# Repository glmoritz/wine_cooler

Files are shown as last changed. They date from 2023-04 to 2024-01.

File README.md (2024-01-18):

# wine_cooler
UPDATE: The hardware is working using this PID script -> https://github.com/glmoritz/tasmota_berry_pid

Control board replacement for an Electrolux Wine Cooler (https://loja.electrolux.com.br/adega-elctrolux--8-garrafas-1-porta-preta-acabamento-em-aluminio---acb08-/p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)

The original control board for this wine cooler is a SH14387 board which is known to present failures during its lifespan. So, instead of ordering a new one for my broken wine cooler I decided to build my own control board using cheap aliexpress components.

The controller will be based on ESP32 Devboard C. This way I can run Tasmota in Thermostat mode and set/monitor all Cooler parameters using MQTT. Tasmota seamslessy integrates with Home Assistant, this way I will have very little work in firmware programming (just recompiling and configuring Tasmota with the correct parameters and then adding the device to Home Assistant).

Tasmota thermostat is very capable. It uses a mixed on/off PID strategy which seems to work well. Time will tell...

Board features:

- The board expects a 12V@6A input, which can be provided by a simple COTS power source.

- Controlled 12V 5A output for driving the peltier board.

- 2x Controlled 12V 200mA output for driving the cold/hot peltier fans.

- 10k NTC input for reading the built in Cooler NTC 

- DS1820 input (https://pt.aliexpress.com/item/4000895660165.html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)

This will be the Thermostat feedback sensor. The built in sensor is installed directly on peltier cell which is always colder than the cooler interior. I am planning to install the DS1820 nearer to the bottles to have a more precise temperature control.

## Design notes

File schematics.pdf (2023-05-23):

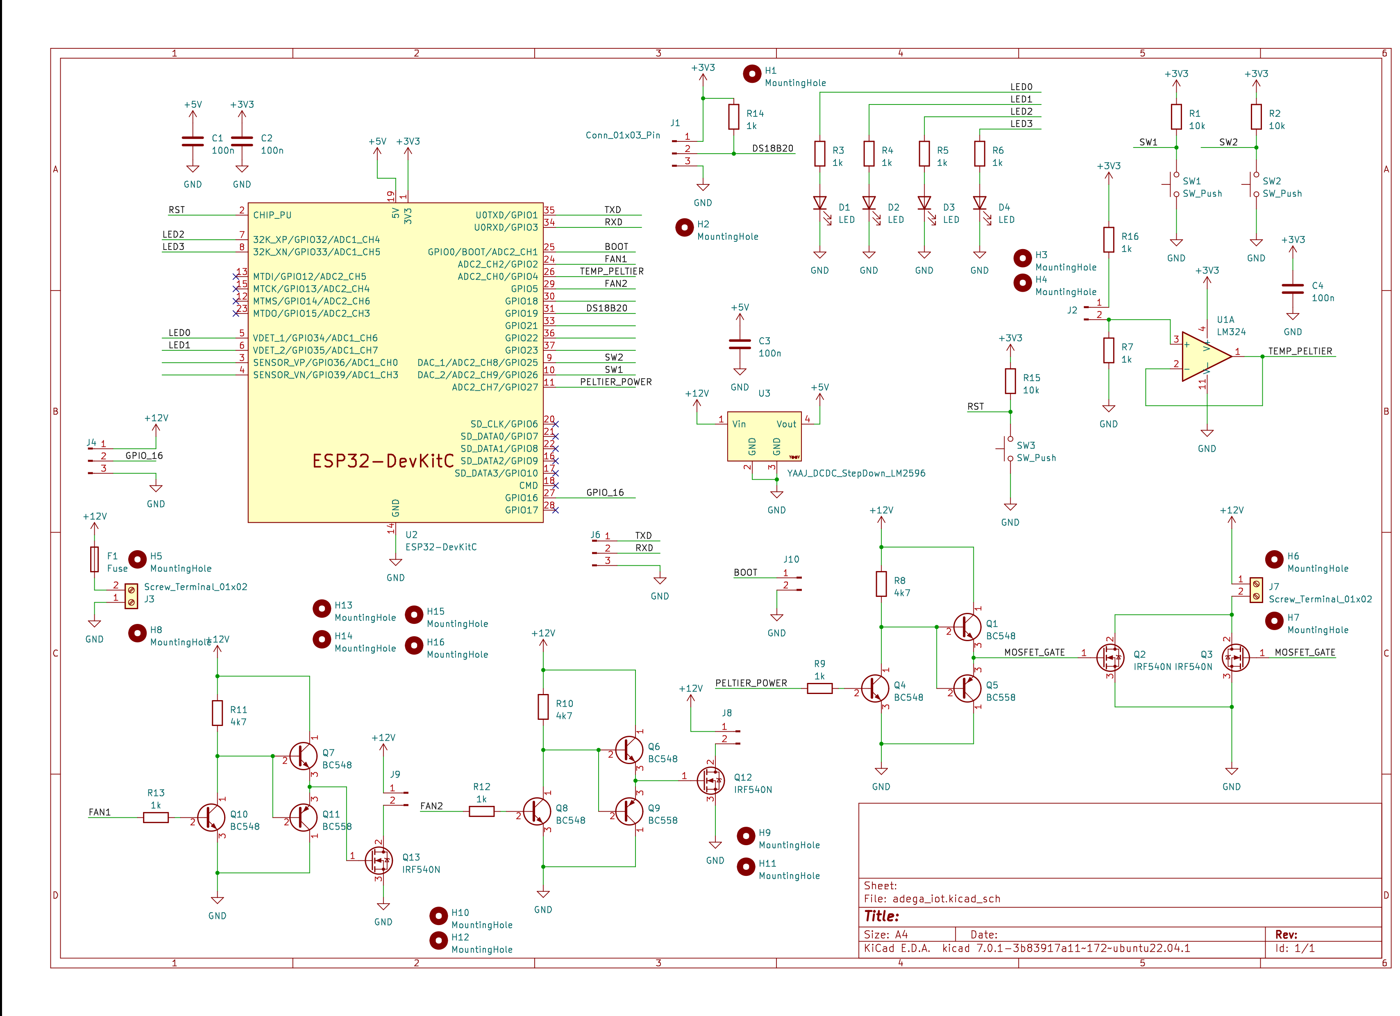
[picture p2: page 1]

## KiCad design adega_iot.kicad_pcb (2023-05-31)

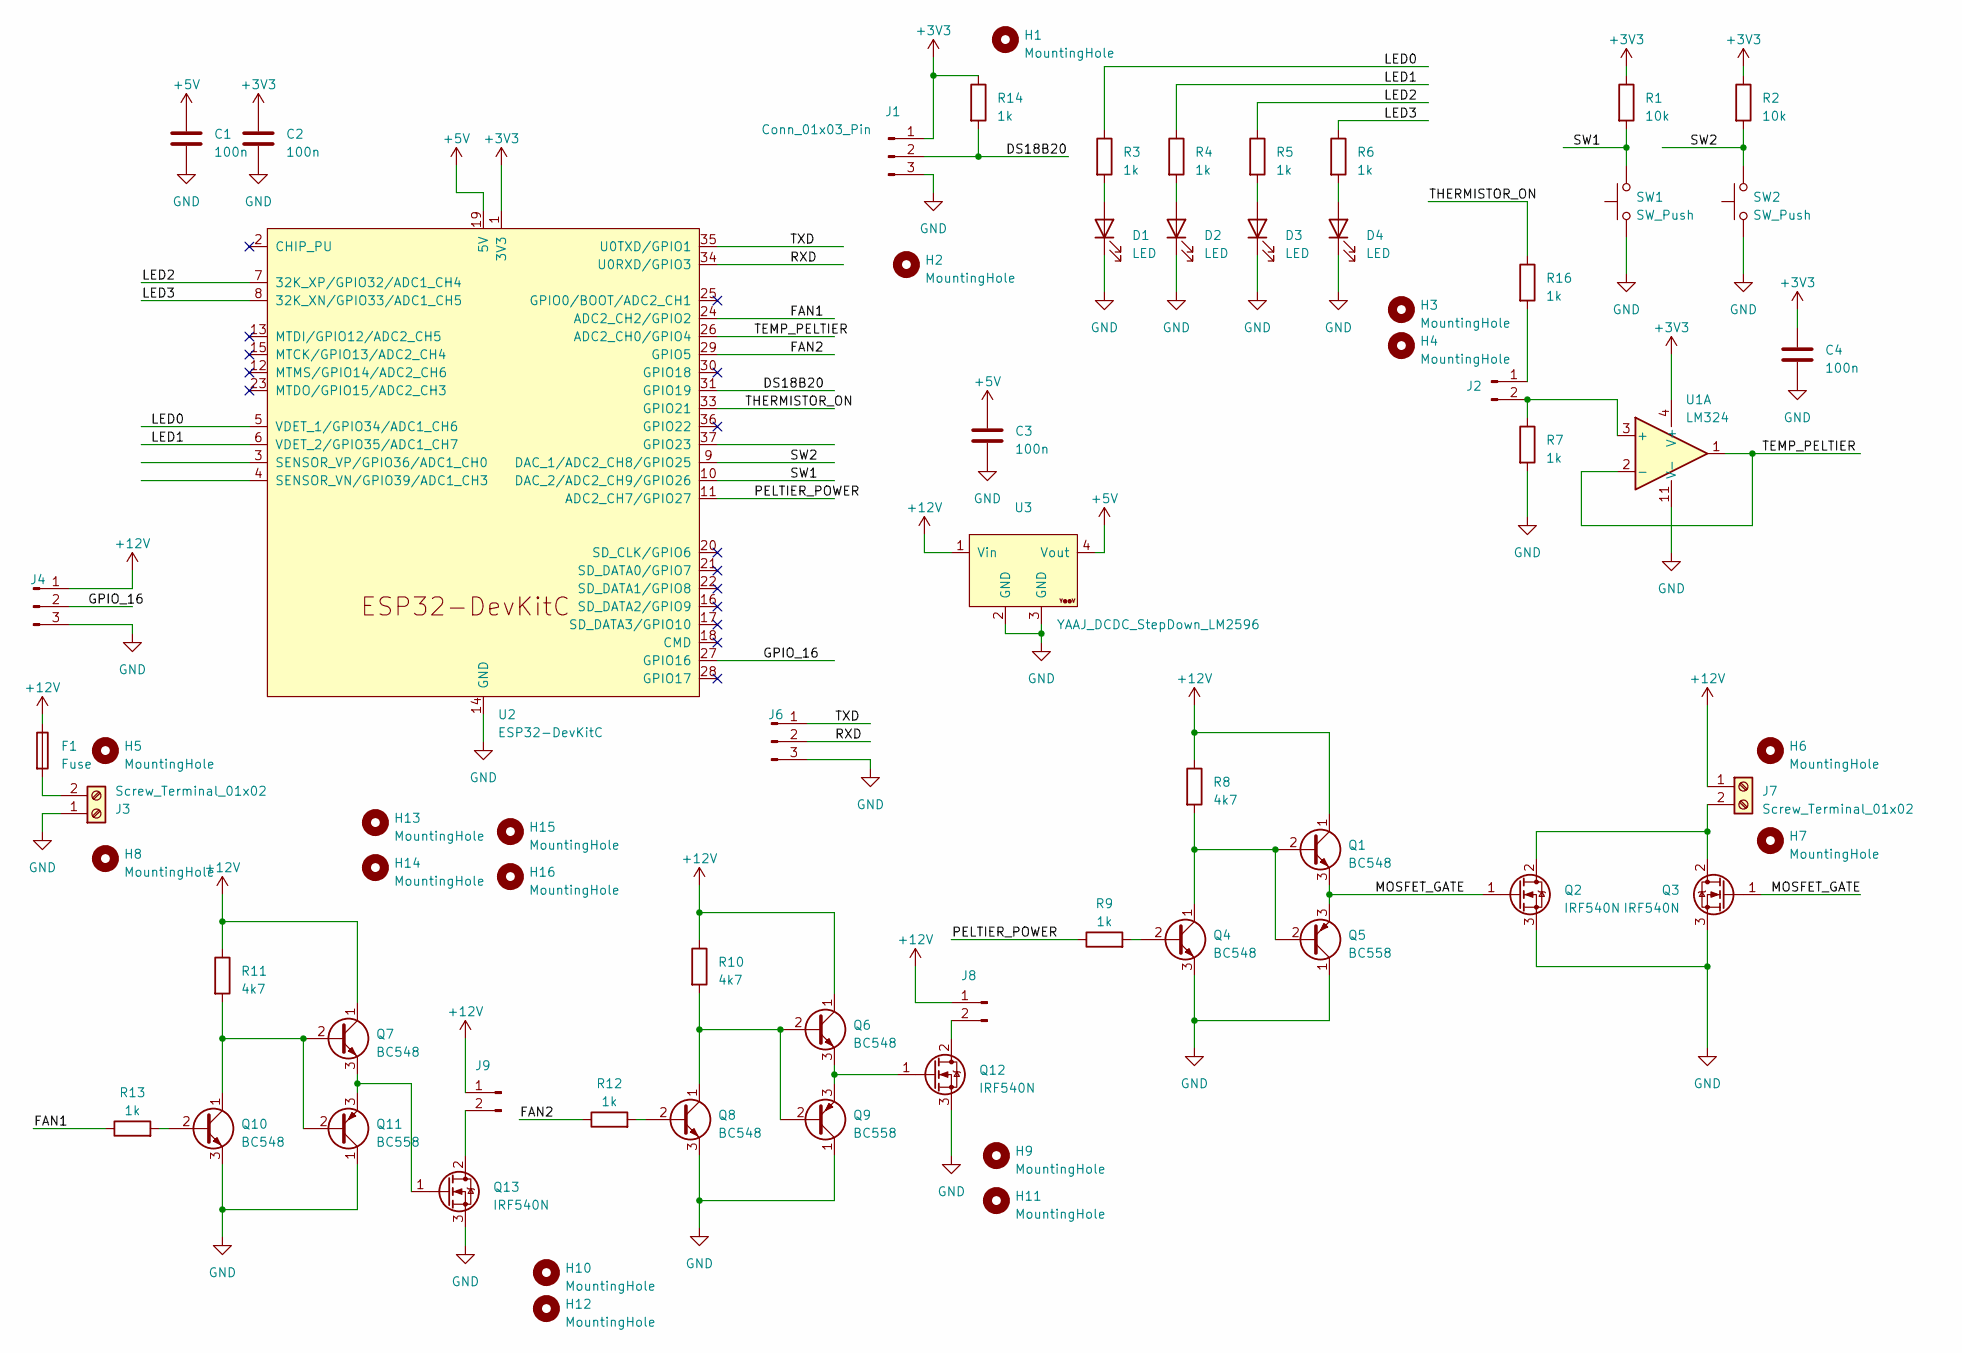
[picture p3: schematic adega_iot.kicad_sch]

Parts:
C1, C2, C3, C4: 100n; C_Disc_D7.5mm_W4.4mm_P5.00mm
D1, D2, D3, D4: LED; LED_D3.0mm
F1: Fuse; Metaltex_fuse_holder
H1, H2, H3, H4, H5, H6, H7, H8, H9, H10, H11, H12: MountingHole; MountingHole_2mm
H13, H14, H15, H16: MountingHole; MountingHole_3.2mm_M3
J1, J4, J6: Conn_01x03_Pin; PinHeader_1x03_P2.54mm_Vertical
J2, J8, J9: Conn_01x02_Pin; PinHeader_1x02_P2.54mm_Vertical
J3, J7: Screw_Terminal_01x02; HANDSON_KF301-2P
Q1, Q4, Q6, Q7, Q8, Q10: BC548; TO-92_Inline_Wide
Q2, Q3, Q12, Q13: IRF540N; TO-220-3_Vertical
Q5, Q9, Q11: BC558; TO-92_Inline_Wide
R1, R2: 10k; R_Axial_DIN0204_L3.6mm_D1.6mm_P7.62mm_Horizontal
R3, R4, R5, R6, R7, R9, R12, R13, R14, R16: 1k; R_Axial_DIN0204_L3.6mm_D1.6mm_P7.62mm_Horizontal
R8, R10, R11: 4k7; R_Axial_DIN0204_L3.6mm_D1.6mm_P7.62mm_Horizontal
SW1, SW2: SW_Push; SW_PUSH_6mm_H7.3mm
U1: LM324; DIP-14_W7.62mm
U2: ESP32-DevKitC
U3: YAAJ_DCDC_StepDown_LM2596

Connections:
+3V3: C2.1, C4.1, J1.1, R1.1, R2.1, R14.1, U1.4 (V+), U2.1 (3V3)
+5V: C1.1, C3.1, U2.19 (5V), U3.4 (Vout)
+12V: F1.1, J4.1, J7.1, J8.1, J9.1, Q1.1 (C), Q6.1 (C), Q7.1 (C), R8.1, R10.1, R11.1, U3.1 (Vin)
/DS18B20: J1.2, R14.2, U2.31 (GPIO19)
/FAN1: R13.1, U2.24 (ADC2_CH2/GPIO2)
/FAN2: R12.1, U2.29 (GPIO5)
/GPIO_16: J4.2, U2.27 (GPIO16)
/LED0: R3.1, U2.5 (VDET_1/GPIO34/ADC1_CH6)
/LED1: R4.1, U2.6 (VDET_2/GPIO35/ADC1_CH7)
/LED2: R5.1, U2.7 (32K_XP/GPIO32/ADC1_CH4)
/LED3: R6.1, U2.8 (32K_XN/GPIO33/ADC1_CH5)
/MOSFET_GATE: Q1.3 (E), Q2.1 (G), Q3.1 (G), Q5.3 (E)
/PELTIER_POWER: R9.1, U2.11 (ADC2_CH7/GPIO27)
/RXD: J6.2, U2.34 (U0RXD/GPIO3)
/SW1: R1.2, SW1.2, U2.10 (DAC_2/ADC2_CH9/GPIO26)
/SW2: R2.2, SW2.2, U2.9 (DAC_1/ADC2_CH8/GPIO25)
/TEMP_PELTIER: U1.1, U1.2 (-), U2.26 (ADC2_CH0/GPIO4)
/THERMISTOR_ON: R16.1, U2.33 (GPIO21)
/TXD: J6.1, U2.35 (U0TXD/GPIO1)
GND: C1.2, C2.2, C3.2, C4.2, D1.1 (K), D2.1 (K), D3.1 (K), D4.1 (K), J1.3, J3.1, J4.3, J6.3, Q2.3 (S), Q3.3 (S), Q4.3 (E), Q5.1 (C), Q8.3 (E), Q9.1 (C), Q10.3 (E), Q11.1 (C), Q12.3 (S), Q13.3 (S), R7.2, SW1.1, SW2.1, U1.11 (V-), U2.14 (GND), U2.32 (GND), U2.38 (GND), U3.2 (GND), U3.3 (GND)
unnamed: D1.2 (A), R3.2
unnamed: D2.2 (A), R4.2
unnamed: D3.2 (A), R5.2
unnamed: D4.2 (A), R6.2
unnamed: J2.1, R16.2
unnamed: J2.2, R7.1, U1.3 (+)
unnamed: F1.2, J3.2
unnamed: J7.2, Q2.2 (D), Q3.2 (D)
unnamed: J8.2, Q12.2 (D)
unnamed: J9.2, Q13.2 (D)
unnamed: Q1.2 (B), Q4.1 (C), Q5.2 (B), R8.2
unnamed: Q4.2 (B), R9.2
unnamed: Q6.2 (B), Q8.1 (C), Q9.2 (B), R10.2
unnamed: Q8.2 (B), R12.2
unnamed: Q10.2 (B), R13.2
unnamed: Q7.2 (B), Q10.1 (C), Q11.2 (B), R11.2
unnamed: Q7.3 (E), Q11.3 (E), Q13.1 (G)
unnamed: Q6.3 (E), Q9.3 (E), Q12.1 (G)

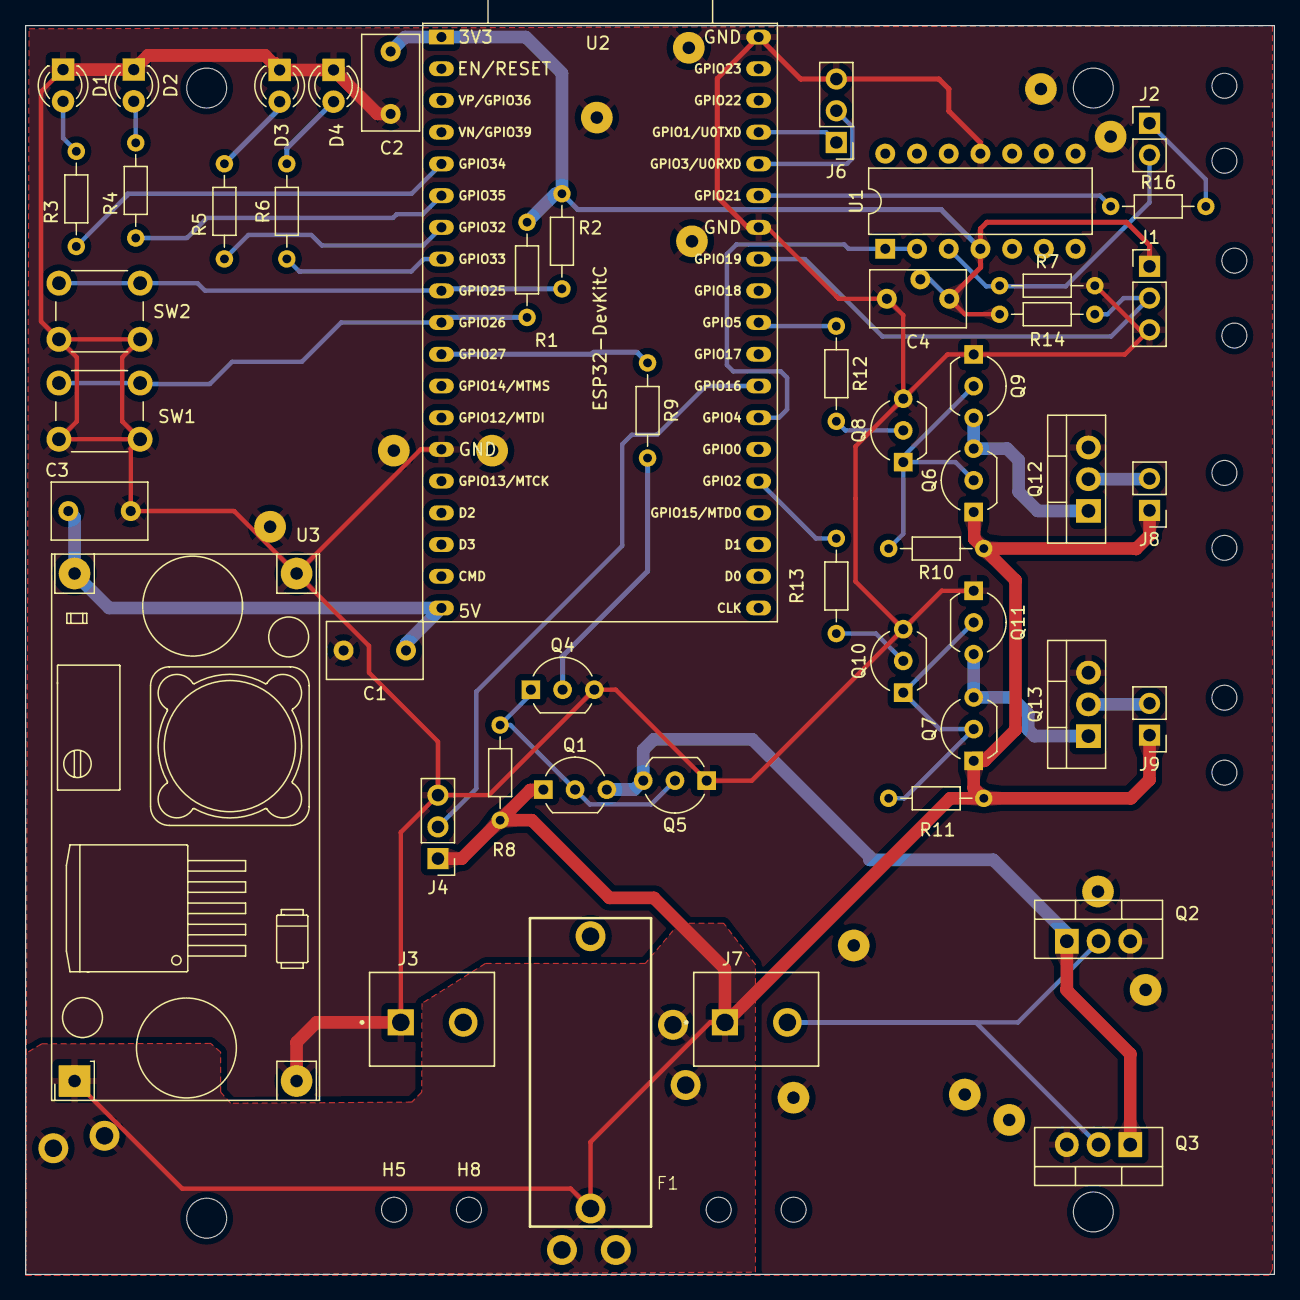
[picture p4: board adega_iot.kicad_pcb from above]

Board: 2 copper layers, 100.0 x 100.0 mm, 66 parts (0 on the bottom side), 38 nets.

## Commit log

2023-04-26 First Version
    [adega_iot.kicad_pcb, adega_iot.kicad_sch]
2023-04-26 Added LM2596
    [adega_iot.kicad_sch]
2023-05-02 adding screw terminals
    [adega_iot.kicad_pcb, adega_iot.kicad_sch]
2023-05-03 Preliminary placement
    [adega_iot.kicad_pcb, adega_iot.kicad_sch]
2023-05-03 partial routing
    [adega_iot.kicad_pcb, adega_iot.kicad_sch]
2023-05-04 Routing Progress
    [adega_iot.kicad_pcb, adega_iot.kicad_sch]
2023-05-05 routing updates
    [adega_iot.kicad_pcb]
2023-05-09 DRC and Teardrops
    [adega_iot.kicad_pcb]
2023-05-10 Added a pullup to DS18B20
    [adega_iot.kicad_pcb]
2023-05-12 Reset Button and NTC pullup
    [adega_iot.kicad_pcb, adega_iot.kicad_sch]
2023-05-23 Fabrication Outputs
    [adega_iot-B_Cu.gbr, adega_iot-B_Mask.gbr, adega_iot-B_Paste.gbr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]
2023-05-30 Added Thermistor on GPIO pin
    [adega_iot.kicad_pcb, adega_iot.kicad_sch]
2023-05-31 bug fixes
    [adega_iot.kicad_pcb, adega_iot.kicad_sch]
2023-05-31 more bug fixes
    [adega_iot.kicad_pcb]
